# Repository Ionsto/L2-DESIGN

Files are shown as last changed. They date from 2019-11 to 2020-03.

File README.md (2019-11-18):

# L2-DESIGN
 Level 2 design coursework, electric skateboard

PLEASE USE THE FOLDER STRUCTURE PROPERLY TO KEEP THINGS EASY TO FIND

USE THIS https://www.overleaf.com/edu/durham#overview get a free account \#blessed
 
## GIT
How to use git for dummies:

https://rogerdudler.github.io/git-guide/

The general idea is that you:
 - *PULL* at the start of work, make some changes locally
 - *ADD* only the key changed files
 - *COMMIT* changes with a descriptive commit message 
 - *PUSH* to give everybody else your changes

You should aim to do small and often commits vs large dumps of changes.
This allows merges to happen easier, and makes everybody life easier.

The Git workflow:

https://www.atlassian.com/git/tutorials/comparing-workflows

The heart of the git system is commits, they are your changes, and they have messages describing what youve done.
How to write a great commit message:

https://chris.beams.io/posts/git-commit/

## LaTeX

Compiled markup language, the compiler can be easily installed via TexMaker.

Resources for latex:

Overleaf has a great set of resources for learning latex, I would recomend you write text - then when you need to know a specific feature look it up.\\
- https://www.overleaf.com/learn
- https://www.overleaf.com/learn/latex/Learn_LaTeX_in_30_minutes#The_preamble_of_a_document

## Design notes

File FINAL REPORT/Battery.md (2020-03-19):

# Battery section outline
First section is headings and sub topics
## Headings
- Introduction
- Capacity
- Charging
- Control system
- Disposal  
# Direction 
### Introduction
- Actual configuration 
- Need for a battery
- Battery types
- Estimated capacity
- Estimated size and volume
### Capacity
- Range
- Gradient
- Estimated efficiency 
- Size
- Weight
- Off the shelf solutions
### Charging
- Dangers
- Mitigations
- Voltages
- Currents
- Charging times
- Use of pre-built chargers
- Need for a parallel - series mux
### Charging MUX
- Whats the purporse
- What are the key goals (safty, supplying power, allowing safe charging)
- Overview of mux circuitry
- Switching technolog
### Control system
- Seperate power supply
- Monitor charge cycles and battery health
- Wake up and monitor voltages
- Control supply MUX
- 
### Disposal
- WEEE
- Take back scheme
- Maintanance and takeback

# Nomenclture:
- S rating for batteries - how many cells in series
- Gravometric density, Wh per kg
- Volumetric density, Wh per litre 

# Direction
## Introduction 
- Battery pack is made of two smaller 6S batteries - battery voltage has increased since the feasiblity report
- Batteries are integral to eletric vehicles
- We chose lithum polymer, much better current suuply and lifespan compared to other chemistrys.
- Estimated minimum capcaity ~180Wh from feasibilty report
- We are going to be useing off the shelf batteries: XXXX XXXX
- Two battereies required to reach line voltage ~50V
- Each battery is aproximately the size xxx,xxx,xxx mm
## Capacity
- Each battery has a caoacity of ~180Wh
## Charging
- Lithium polymer is very dangerous, lots of mitigations requried to make them "safe" see faliure mode analysis
- Instead of designing and building a charging circuit - use an off the shelf solution
- We are going to use an afordable charger, model XXX which can charge one battery in X hours.
- The charger can only charge at a rail voltage of 24V - so our two batteries need to be chaged parralel
- We will need a system to take them from series to parrralel
## Control system
- To control the battery system we need an independent control system
- The control system will be based around a low power microcontroler
- There are 4 states as shown in the control flow diagram
- The control micro will monitor the battery pack and will control the series/parralel state.
- The mux will be eletrically controled and isolated from the battery micro
- The control circuit will have a serial connection to the drive micro - along with a heartbeat connection
## Battery mux
- Mux circuitry
- How the mux will make the circuit safer
- The charger can't charge in series - voltage is too high
- The balancing leads are required to keep the cells from degrading from overdischarge
- Switching technology chosen is solid state power switches (high side switching fet based systems).
- Fets > Relays and mechanical switches as they are resistant to vibration and wont contact weld shorted

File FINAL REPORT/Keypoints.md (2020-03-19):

# Key points we want to talk about for the report
## Introduction
## Business case
## Decision matrices

## Drive belt

## Battery

## Electrical control systems

## Final words

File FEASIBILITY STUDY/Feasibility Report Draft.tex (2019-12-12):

\documentclass[journal,10pt]{IEEEtran}
\usepackage{amsmath}
\usepackage{graphicx}
\usepackage{float}
\usepackage{comment}
\usepackage{setspace}
\usepackage{caption}
\usepackage{hyperref}
\usepackage[T1]{fontenc}
\doublespacing
\title{ 
\begin{huge}
\textbf{L2 Design Feasibility Report: Electric Skateboard} 
\end{huge} }
\author{Toby Ashton, Jacob Black, Hugo McCartney, Haydn Lisk, Edward Street, Sam Sutcliffe}
\begin{document}
\maketitle
\tableofcontents
\newpage
\section{Executive Summary}
        This project concerns the design and construction of an electric skateboard based on a traditional longboard.
\section{Introduction}
        This project's scope consists of designing an electric skateboard capable of carrying a large male for daily transport. A longboard was supplied which will be modified to produce the final product. 
\section{Board}
    \subsection{Overview}
        The board provided was a 'Mindless Raider I model (34’’ x 8’’)’\cite{boardModel}. The deck was modelled in SOLIDWORKS and assembled with a library model of the trucks \cite{trucksCAD} - this allowed a Finite Element Method (FEM) analysis to be performed. Material properties were taken for maple wood, as it is the main board material. Fig \ref{fig:Board_Rendering} shows a rendering of the final concept \cite{shoesCAD}. 
        \begin{figure}[H]
                \centering
                \scalebox{0.25}{}
                \caption{
                Rendering of Skateboard}
                \label{fig:Board_Rendering}
            \end{figure} 
    \subsection{Component Arrangements}
        Several arrangement options for the electrical components were explored, subject to the following limiting factors:
        \begin{itemize}
            	\item Ground Clearance
            	\item Transmission Efficiency
            	\item Balance 
            	\item Rider Comfort
            \end{itemize}
        \begin{figure}[H]
                \centering
                \scalebox{0.30}{}
                \caption{Concept A}
                \label{fig:ConceptA}
            \end{figure} 
        \begin{figure}[H]
                \centering
                \scalebox{0.19}{}
                \caption{Concept B}
                \label{fig:ConceptB}
            \end{figure}  
        \begin{figure}[H]
                \centering
                \scalebox{0.19}{}
                \caption{Concept C}
                \label{fig:ConceptC}
            \end{figure} 
        \begin{figure}[H]
                \centering
                \scalebox{0.19}{}
                \caption{Concept D}
                \label{Fig:ConceptD}
            \end{figure} 
        \begin{figure}[H]
                \centering
                \scalebox{0.19}{}
                \caption{Concept E}
                \label{Fig:ConceptE}
            \end{figure}
    \subsection{Structural Analysis}
        %Rider load was assumed to total 1100N, applied over two 10cmx10cm areas at appropriate positions on the board. An additional load of 80N was applied at the centre of the wheelbase to model the weight of the electrical components.The simulation computed the maximum Von-Mises stress to be approximately 31.69MPa, located at the joint between the truck and the board, as shown in the figures below.
        \begin{figure}[H]
            \centering
            \scalebox{0.3}{}
            \caption{FEM Von Mises Stress Analysis of Top Surface of the Board
            }
            \label{fig:stressTop}
        \end{figure}
        \begin{figure}[H]
            \centering
            \scalebox{0.35}{}
            \caption{FEM Von Mises Stress Analysis of Bottom Surface of the Board
            }
            \label{fig:stressBottom}
        \end{figure}
        %Comparing this to the yield strength of maple wood, approximately 65.5MPa \cite{materialProperties}, a Factor of Safety value of approximately 2.1 was calculated. A further simulation was performed with the rider's load scaled up by this FOS, and the load located at a single 10cmx10cm area at the centre of the wheelbase. Maximum displacement was calculated as approximately 18.19mm (shown below). 
        \begin{figure}[H]
                \centering
                \scalebox{0.35}{}
                \caption{Displacement Contour of Board When Put Under Maximum Loading
                }
                \label{fig:Displacement}
            \end{figure}
        %With the unloaded board height of 110mm, this allows a minimum ground clearance of approximately 91.8mm - this was considered acceptable as the electrical components will have a max height of 45.9mm considering a FOS of 2.
    
\section{Powertrain}
    \subsection{Transmission}
        \subsubsection{Gearing}
            Gears provide a vast array of gear ratios but the large range of output speeds of motors makes large gear ratios unnecessary.
        \begin{figure}[H]
            \centering
            \scalebox{0.125}{}
            \caption{Arrangement with gears}
            \label{fig:DrivetrainChain}
        \end{figure}
        \subsubsection{Hub Motor}
            Hub motors are contained in the wheels of the skateboard, offering many advantages including quietness, low maintenance and sleek appearance.
            However as they have no gearing and have limited space, they provide less torque than other drives. %\[cooling?, wheel customization, ride- thin polyurethane]
        \subsubsection{Chain}
            Using a chain drive is the most efficient way to transmit power amongst the options covered, with a typical efficiency of 98\%. \cite{Mechanical_Power_Transmission} However, high maintenance is required due to the need for lubrication to prevent wear and corrosion. 
        \subsubsection{Belt}
            Due to the elasticity of toothed rubber belts, this option provides low noise and vibration, and efficient power transmission. Furthermore, they require relatively low maintenance and have a long lifespan making this preferable.
        \begin{figure}[H]
            \centering
            \scalebox{0.14}{}
            \caption{Arrangement with Belt or Chain}
            \label{fig:Drivetrain2}
        \end{figure}
        \begin{figure}[H]
            \centering
            \scalebox{0.13}{}
            \caption{Arrangement with Belt attached to trucks}
            \label{fig:Drivetrain3}
        \end{figure}
        
    \subsection{Motor}
        \subsubsection{Required Parameters}
        The main requirements of the motor at 8$ms^{-1}$, with a slope of 10$^{\circ}$ and 1$ms^{-2}$ acceleration using equations bellow are:
        \begin{itemize}
        	\item Size- The motor must fit under the board and be relatively lightweight
        	\item Torque- 13Nm at the wheel 
        	\item Speed- The $K_{v}$ motor parameter should be 250 eqn
        	\item Power- 2000w assuming no acceleration uphill at 8$ms^{-1}$
        \end{itemize}
        \begin{figure}[H]
            \centering
            \scalebox{0.5}{}
            \label{fig:equations}
        \end{figure}
        
        %\begin{gather}
        %    F = F_{Rolling Resistance} + F_{Acceleration} + F_{Gravity}\\
        %    F_{Acceleration} = Mass \times Acceleration\\
        %    F_{Gravity} = Weight \times sin(Slope Angle)\\
        %    F_{Rolling Resistance} = 4.64N\\
        %    Torque = F_{Total} \times R_{Wheels}\\
        %    Wheel RPM = \frac{Velocity (ms^{-1})}{Radius}\times \frac{60}{2\pi}\\ 
        %    Motor Power = \frac{F_{Total} \times Velocity (ms^{-1})}{Efficiency}
        %\end{gather}
        \subsubsection{AC Motor}
            AC induction motors have excellent efficiency, reliability and durability. However, using DC supply would require a variable frequency inverter to produce AC speed control. 
        \begin{figure}[H]
            \centering
            \scalebox{0.25}{}
            \label{fig:AC_Curve}
            \caption{AC Motor Curve \cite{AC_Motor_pic}}
        \end{figure}
        \subsubsection{DC Brushed Motor}
            Using a commutator allows a motor to be run from a DC supply but using carbon brushes adds a large amount of friction and varying the speed of this type of motor is harder, especially if two motors were implemented and run synchronously.
        \subsubsection{DC Brushless Motor}
            With an electronic speed controller a motor can be run from a DC supply with speed control and without a commutator meaning less friction so greater efficiency, longer lifespan and reduced weight for the same output power. This motor family also gives a large staring torque, enabling the board to accelerate quickly at low speeds \cite{AC_Motor}. For these reasons it was decided a DC brushless motor would be used.
    \section{Battery}
    A compact and quickly rechargeable battery is required. A supply rail of 24V is common for consumer electronics and will not require high voltage safety precautions. Battery charge capacity (amp-hours) and energy capacity are used roughly interchangeably due to the constant supply voltage for ease of calculation but will be annotated with the units strictly.
        \subsubsection{Capacity}
            The larger a battery network's capacity, the heavier and more expensive it becomes.Two main considerations regarding required capacity are range and lifespan. Range is be determined by average daily usage (a 1.5 km round trip between Butler and Science sites, (Fig. \ref{fig:route}) and expected charge frequency (assumed once a week).
            \begin{figure}[H]
                \centering
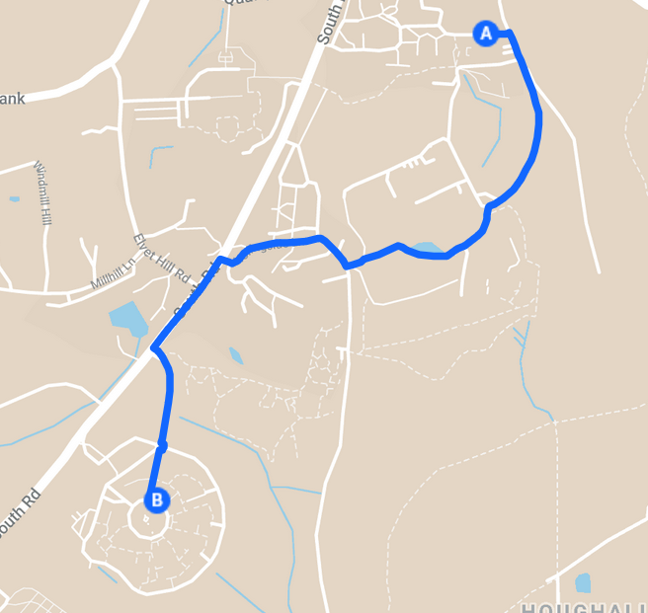
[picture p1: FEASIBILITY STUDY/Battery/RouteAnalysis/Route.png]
                \scalebox{0.5}{}
                \caption{Typical Daily Route}
                \label{fig:route}
            \end{figure}
            Extra energy considerations will be needed for the range as there is a relatively large height change throughout the route.
            Elevation and gradient variations can be seen in the graphs below, with data sourced from various GPS public databases via an online website \cite{GPSDatabase}.
            Fig \ref{fig:elevation} shows the elevation of the route and makes a difference for the maximum capacity needed.
            Fig \ref{fig:gradient} shows the gradient of this route, which will effect the maximum torque required.
            \begin{figure}[H]
                \centering
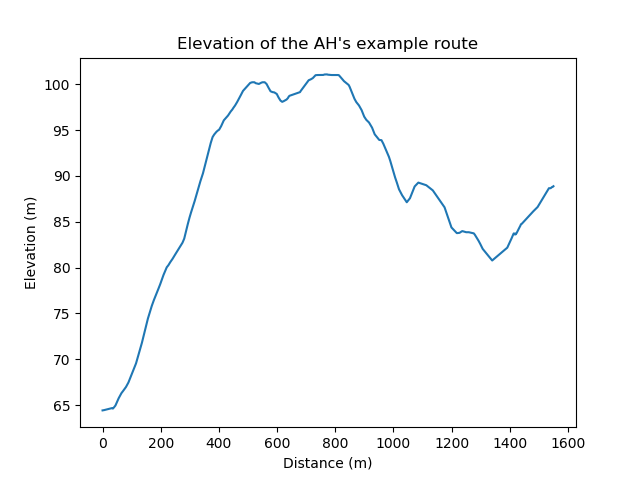
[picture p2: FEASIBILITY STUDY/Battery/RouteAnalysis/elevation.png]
                \scalebox{0.5}{}
                \caption{Elevation of Route}
                \label{fig:elevation}
            \end{figure}
            \begin{figure}[H]
                \centering
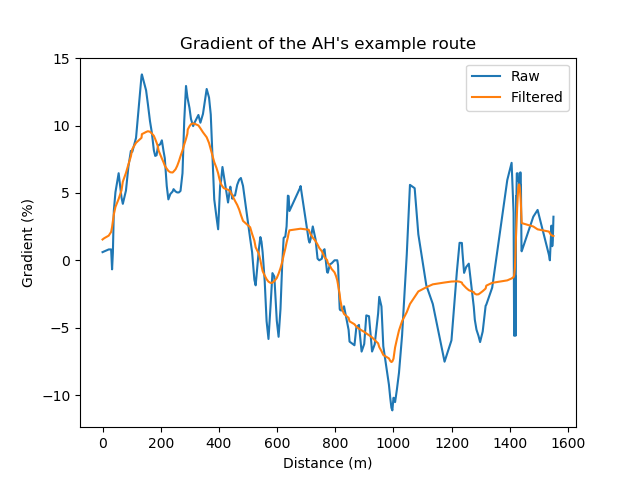
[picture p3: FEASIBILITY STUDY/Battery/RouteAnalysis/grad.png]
                \scalebox{0.5}{}
                \caption{Gradient of Route}
                \label{fig:gradient}
            \end{figure}
            Total elevation change consists of 50m uphill and 25m down (heading south). Energy requirements are modelled as a simple vehicle hoist to give an estimate (Energy = $mg\Delta h$). Total vertical ascent over the trip is 75m, so approximately 90kJ (25Wh) more energy will be required than with a flat route.
        \subsubsection{Energy Requirement Estimates}
            10Wh/mile (based off electric bike: 12Wh/mile)
            Total Energy of Journey (including vertical): 37Wh
            Per Week Consumption: 5 x 37.5Wh = 185Wh
            -Absolute Minimum Required Capacity of 185Wh
        %\subsubsection{Charging}
            %Charging the battery is a complex concern, as specific charging circuits are required to prevent damage to the system. This is particularly true of modern batteries due to the large release of heat associated with large energy transfers.
        \subsubsection{Lifespan}
            \begin{figure}[H]
                \centering
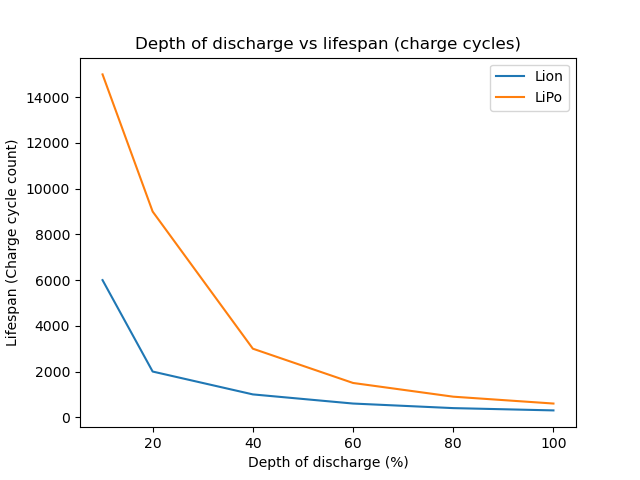
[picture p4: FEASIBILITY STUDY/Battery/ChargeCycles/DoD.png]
                \scalebox{0.5}{}
                \caption{Lifespan vs DoD (Depth of Discharge)}
                \label{fig:DoD}
            \end{figure}
            \cite{BatteryLifespan} 
            \ref{fig:DoD} illustrates the superior lifespan at comparable discharge depths.
            Lithium-ion batteries have a life cycle of approximately 800 cycles at 50\% DoD, whereas Lithium Polymer cells perform better at approximately 2000 charges at the same DoD - we will be using LiPo for this reason. Given that the capacity required at 100\% DoD is 185Wh, a 370Wh capacity is needed to achieve 50\% DoD for a full use.
        \subsubsection{Rate of Charge}
            Lithium polymer charges at a constant rate until near capacity, at which they slow down exponentially. General guidelines suggest that the charge rate should not exceed 1C [charging the total charge in one hour] to ensure optimal battery life. Ideally, the battery will charge from 50\% to full overnight. This will be achievable at a sub 1C rate [15 amp charger], which allows it to recharge from consumer wall sockets.
        \subsubsection{Battery Size}
        Battery volume and weight are limiting factors wrt. capacity. Volume affects how the components can be arranged on the board, while weight directly impacts the board's performance.    
        Using the calculated capacity the volume and mass can be calculated with the volumetric \& graviometric density. Using values from \ref{fig:Battery Size}, the volume comes to about 1.2 Litres with a mass of 2.3Kg.
            \begin{figure}[H]
                \centering
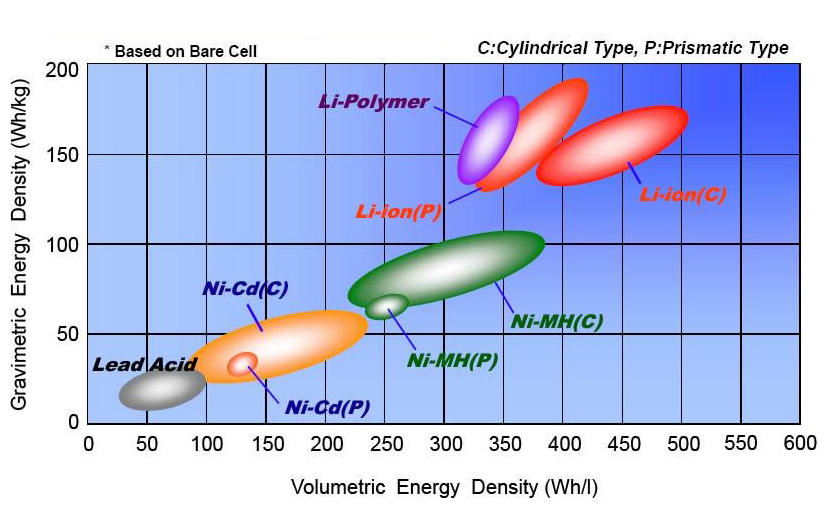
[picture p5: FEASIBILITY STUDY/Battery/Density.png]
                \scalebox{0.40}{}
                \caption{Battery size and energy density \cite{BatteryDensity}}
                \label{fig:Battery Size}
            \end{figure}
\section{Trucks}
    \subsection{Operating Terrain}
        The board will be operating over mostly smooth surfaces - however, disturbances such as uneven patches of road, litter and debris will still be present. At high speeds, low frequency oscillations (4-10Hz, called 'speed wobble' \cite{speedwobble}) build and begin to impede rider control. A suspension system is thus required to minimise these effects.
    %\subsection{Speed Wobble}
        %This phenomenon consists of unpredictable vibrations (approx. 4-10Hz) induced in the board when running at high speed – if neglected, these oscillations could directly affect the user’s ability to control the board, reducing rider comfort and potentially resulting in injury. 
    \subsection{Potential Solutions}
        Buying existing truck suspension systems would free up development time, however due to availability constraints, a bespoke design may be necessary.
        Several patented designs exist, as shown in figures \ref{fig: Spring Idea}, \ref{fig: Seperate Spring Idea} and \ref{fig: Hanger Idea}. Fig.\ref{fig: Spring Idea} shows an ideal solution, with the decision to purchase or manufacture being dependent on labour and budget constraints yet to be determined.
        \begin{figure}[H]
            \centering
            \scalebox{0.22}{}
            \caption{%Credits: Seismic Skate 
            Shock Absorber Suspension
            \cite{spring_idea} \cite{shockabsorber}}
            \label{fig: Spring Idea}
        \end{figure}
        \begin{figure}[H]
            \centering
            \scalebox{0.22}{}
            \caption{%Credit: US Patent 4,176,850 'SKATEBOARD TRUCK WITH INDEPENDENT WHEEL SUSPENSION'
            Independent Wheel Suspension
            \cite{separate_spring}}
            \label{fig: Seperate Spring Idea}
        \end{figure}
        \begin{figure}[H]
            \centering
            \scalebox{0.5}{}
            \caption{%Credit: Avenue Trucks 
            Hanger Suspension
            \cite{hanger}}
            \label{fig: Hanger Idea}
        \end{figure}
\section{Wheels}
    \subsection{Overview}
        Various factors affect the wheel design – rolling resistance is affected by the wheel and bearing materials, with torque transferred dependent on the radii and material of the driven wheels.
    \subsection{Wheel Materials}
        Longboard wheels are typically made from polyurethane, which achieve a $\mu_{rolling}$ in the range 0.04-0.08 \cite{wheel_data}. While this is sufficiently small to provide low rolling resistance (see calculations below), polyurethane only provides a $\mu$-static of ~0.2, limiting the torque that can be transferred to the road. This can be improved by using rubber for the driven wheels as rubber achieves a $\mu$-static in the range of 0.35-0.45, providing an increase in torque transmitted of 75-125\%.
    \subsection{Bearing Materials}
        Longboard bearings come in three different material families: steel, titanium and ceramic. Ceramic (Silicon Nitride) has a Brinell hardness 1479 $kg/mm^{2}$ \cite{ceramic_data1}, approximately 640\% greater than AISI-52100 steel \cite{steel_data} and ASTM-7 Titanium \cite{titanium_data}, leading to reduced energy loss from elastic deformation.  However, Silicon Nitride exhibits a yield strength of 170MPa \cite{ceramic_data2}: approximately 64\% less than steel and titanium. Ceramic is thus inadvisable as the board will be used in an environment where it is expected to suffer shocks. Additionally, ceramic bearings cost significantly more than steel and titanium, the former often in the \$90-\$150 range, as opposed to \$15-\$20 and \$30 for steel and titanium respectively. As steel and titanium perform similarly, the latter’s corrosion resistance suggests that it is the optimal type as less maintenance will be required. 
    \subsection{Wheel Dimensions}
        Longboard wheels vary in diameter between 60-100mm with a contact-patch width of approx. 30mm. Larger wheel radii provide greater top speed and smoother ride, with smaller radii producing greater mechanical advantage. 
        Wheel diameter is selected to provide the desired torque when driven by the chosen motor.
        %Depending on the output of the motor and the required road-torque, the appropriate wheel size can be selected.
    \subsection{Estimates of Rolling Resistance}
       % \begin{equation*}
       % \resizebox{\columnwidth}{!}{%
           % $F_{resistive} = (\mu _{static}  -  r_i sin(\alpha) \cos(\arcsin(\frac{r_f}{r_i}))  +  r_f %cos(\alpha)(\frac{F_{load}}{r_o – r_i})$%
    %        }
    %    \end{equation*}
    \begin{figure}[H]
        \centering
        \scalebox{0.45}{}
        \label{fig:WheelEquations}
    \end{figure}
    %Static
    %$F_{res-rubber} \approx 10.98N	
    %\\*F_{res-polyurethane} \approx 4.88N
    %\\*F_{res-total-static} = 2 F_{res-rubber} + 2 F_{res-polyurethane} = 31.72N $
    %\\*Dynamic
    %\\*$F_{res-rubber} \approx 0.37N	
    %\\*F_{res-polyurethane} \approx 1.95N
    %\\*F_{res-total-dynamic} = 2 F_{res-rubber} + 2 F_{res-polyurethane} = 4.64N$
    \cite{Combined_Resistance} 
    
\section{Control}
    \subsection{Overview}
    	Complex electronic systems require control units for operation.
    	Three aspects of control must be designed for; the user interface, battery management, and motor/drive train control.
    	In this application, the one-off nature of the product lends itself to use a micro-controller for control, rather than bespoke hardware. Microcontrollers can alter their functionality with speed and ease, due to the volume of support documentation available. Due to time and budget constraints, it may prove more effective to use existing circuit modules such as these than implementing a bespoke design.
    \subsection{User Interface}
        \begin{figure}[H]
            \centering
            \scalebox{0.2}{}
            \caption{Market Leader's Remote Control}
            \label{fig:Boosted Remote}
        \end{figure}
        \begin{figure}[H]
            \centering
            \scalebox{0.2}{\includegraphics{"./Control/Pressure Pads
            Labelled".png}}
            \caption{Dual Pressure Pad Control}
            \label{fig:Pressure Pads}
        \end{figure}
            
    	\subsubsection{Throttle Control}
    	    To ride safely, the user requires rapid and intuitive speed selection.
    		The market leader utilises a handheld wireless controller (as shown Fig.\ref{fig:Boosted Remote} \cite{BoostedRemote}) which also relays status information to the rider.
    		A potential solution to this is a dual pressure pad control system, pictured in Fig.\ref{fig:Pressure Pads} \cite{PressurePads}.
            
    	\subsubsection{Status Meters}
    		The rider must know the remaining range/time of the board. The current market leader uses an array of LEDs on its controller for status information. This can be improved by using 7 segment displays or a small LCD, allowing for quantitative data to be shown to the rider. (shown in Fig.\ref{fig:7 seg} \cite{7seg} and Fig.\ref{fig:LCD} \cite{LCD}).
    		
    	\begin{figure}[H]
            \centering
            \scalebox{0.4}{}
            \caption{7 Segment Displays}
            \label{fig:7 seg}
        \end{figure}
    	\begin{figure}[H]
            \centering
            \scalebox{0.4}{}
            \caption{Arduino LCD}
            \label{fig:LCD}
        \end{figure}
    \subsection{Battery Management}
    	Care must be taken to ensure that during normal operation the battery is charged safely.
    	This includes tracking the number of charge cycles, as well as the temperature, with a view to disabling the system if the battery is no longer in a safe state.
    	
    		%General guidelines suggest charging at no faster than 1C for optimal battery lifetime, meaning a 1300maH battery is charged at 1.3A for a duration of 1 hour.
    		%Discharge ratings vary depending on the battery, a typical hobby grade battery used for multi-rotors and helicopters boast a continuous draw of 40-50C, with a 10s burst of 90-120C, much higher than the charging rating.
    		%The number of cycles must be counted, as well as the current battery temperature to ensure that the battery is in a healthy state whenever in use.
    		%This includes preventing charging when the battery has reached the end of its operational lifetime.
    		%If regenerative braking is pursued, the circuitry must be carefully controlled so that the charging current is not exceeding these values.
    \subsection{Motor Control}
    		Since a DC Brushless motor is being used, more complex control methods are required compared to DC brushed motors.
    		This circuitry is available off the shelf, called 'Electronic Speed Controllers' and are available in a range of specifications.
    		Control of these circuits is by pulse width modulation or serial interface, varying by manufacturer, signals that can be generated simply with a microcontroller.
    		This circuit could be designed by hand, however due to complexity, and competitive pricing, it may prove a more effective choice to purchase an existing ESC.
    	%\subsection{Feedback}
    		%text goes here 
\section{Conclusion}
From our research, a number of design conclusions have been drawn: a belt-drive and brushless DC motor were selected for optimal efficiency, while rubber wheels were chosen for the driven axle due to their improved grip over polyurethane. Titanium bearings offer a compromise between performance and durability, with the final component layout providing the optimal trade-off between efficiency, ground clearance and rider comfort.

\bibliographystyle{IEEEtran}
\bibliography{IEEEabrv,bibliography.bib}

\end{document}

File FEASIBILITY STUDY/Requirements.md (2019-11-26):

# Project key points
## Requirements
- Makes minimum distance in one charge
- Hold max load - 1000N
- Charges overnight
- Constant speed uphill (South road 12% grad)
- Throttle control & dead mans switch
- Battery metre
- Easy / limited maintenance
- Waterproof housing for electronics
- Safety
  - Components secured safely
  - Suspension to protect against small bumps
- Comfortably portable / light enough to carry
- Driven wheels must provide sufficient grip for efficient power transfer
- Driven wheels achieve sufficient torque at road surface to propel board
- Non-driven wheels must provide low resistance whilst retaining ability to steer
- Bearings must provide minimal resistance to motion and be capable of withstanding stresses of normal operation

## Desired
- Goes further with one charge
- Holds more load (i.e backpack & laptop)
- Fast charging sub 1 hour
- UI, Variable speed, Acceleration control, low power control (wireless handheld device) 
- No extra lubricating needed
- Corrosion resistant
- Nice efficient housing - protective casing
- Varying suspension (manual or active)
- Efficient suspension for smooth rides
- Mass less than 10kg
- Bearings should require as little maintenance as possible
- Wheels should be durable enough to require infrequent changes
- Wheels should be capable of running on non-concrete/tarmac surfaces for short periods

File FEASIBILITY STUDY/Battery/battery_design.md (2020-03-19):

# Battery overview
## Battery picked
Two 6S batteries are more affordable to find, and allow for the batteries to be placed in disparate locations
There is also the thermal dissapation benifits for having two seperate batteries.
We picked this battery as it has roughly half the voltage we needed, and was small enought that it could fit in the encolsure.

https://www.banggood.com/ZOP-POWER-22_2V-8000mAh-60C-6S-Lipo-Battery-With-XT60-Plug-For-RC-Model-p-1328629.html

Stats:

- Watt hour capacity: 177.6Wh each
- Cell count: 6S
- Voltage: 22.2V
- Size: 90x46x158mm
- Mass: 1.24Kg

2 batteries in parallel, 355.2Wh

The batteries will be in series, so the capacity will be 178Wh together, but the operating voltage will be will be 44.4V.

## Battery charging
https://electronics.stackexchange.com/questions/115795/charging-batteries-in-parallel-when-they-are-connected-in-series-in-the-circuit
Since we have two seeprate batteries that are being used in parralel, we will either need a charger that can handle a 12S system or we will have to do some TDMA parralel charging.
https://www.flitetest.com/articles/Parallel_Charging_Your_LiPo_Batteries
Charger: CHANGED
https://www.banggood.com/ToolkitRC-URUAV-M800-300W-15A-DC-Smart-1-8S-Lipo-Battery-Balance-Charger-Discharger-With-Voltage-Servo-Checker-Receiver-Signal-Tester-Quick-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
This charger has a higher current rating - to drop charge times (did some more maths).
OLD charger: https://uk.banggood.com/SKYRC-e680-80W-8A-ACDC-Balance-Charger-Discharger-for-1-6S-Lipo-Battery-p-1526977.html?ID=47184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

## Battery charging mode 
When in operation, the  batteries are in series to get the correct operating voltage, but for charging they need to be in parralel for the charger to work.

## Battery microcontroller
Low power, separate coin battery supply, min lifespan 5 years
https://www.digikey.co.uk/product-detail/en/stmicroelectronics/STM8L152C6T6/497-10512-ND/2269726

Power supply CR2032 - 225 mAh, 3V nominal

LED indicator:

- Off - hibernating
- On - functioning
- Blinking - dead

Battery status monitor:

- 2 ADC, voltage
- 1 Ammeter, current

Battery capacity line, report both battery voltages to arduino
Battery draw line, report current usage

## Battery states
Battery system state

- Hibernation (battery isolated,LED indicator)
- Idle state (battery live, V+S,V-S, V+P, V-P all off)
- Charge state (V+P, V-P on, V+S,V-S off)
- Drive state (V+P, V-P off, V+S,V-S on)
- Battery disabled state (All off, LED indicator) - wake Arduino state reason?

## Battery switch
Used multiple N channel power MOSFETs as a high side switch

Use gate drivers: https://www.analog.com/en/about-adi/news-room/press-releases/2017/fast-60v-high-side-n-channel-mosfet-driver-provides-100-duty-cycle-capability.html
LTC7004 

Use power mosfets
FDC6324L

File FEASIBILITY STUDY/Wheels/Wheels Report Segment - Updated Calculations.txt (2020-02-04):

Wheels Section
Many factors affect the choice of wheels – rolling resistance is affected by the materials of the
wheels and bearings, with the ability to transfer power dependent on the radii and material of the
driven wheels.
Commercial longboard wheels are typically made from polyurethane, with construction normally
consisting of a hardened plastic core with the outer layers and surface of polyurethane. This material
achieves a μrolling in the range of 0.04-0.08 – while this is sufficiently small to provide low rolling
resistance, polyurethane also only provides a μstatic of ~0.2, limiting the amount of torque than can
be transferred from the motor to road surface. This can be ameliorated by using rubber for the
driven wheels as rubber achieves a μstatic in the range of 0.35-0.45, allowing for an increase in torque
transmitted of 75-125%.
Bearing materials for longboard wheels come in three different material families: steel, titanium and
ceramic. Whilst exact values of frictional resistance are difficult to find, comparisons can be
extrapolated from their material properties. Ceramic (Silicon Nitride) has a Brinell hardness 1479
kg/mm2, an increase of approx. 640% over that of AISI 52100 steel and ASTM 7 Titanium 1. This would
suggest much less energy lost from elastic deformation. However, Silicon Nitride also exhibits a yield
strength of 170MPa: approx. 64% less than steel and titanium. As such ceramic may be unadvisable
as the board will be used in an environment not dedicated to skateboarding and is likely to suffer
various shocks. Additionally, ceramic bearings cost significantly more than steel and titanium, the
former often in the $90-$150 range, as opposed to $15-$20 and $30 mark for steel and titanium
respectively. Due to the similar properties of steel and titanium bearings, the latter’s corrosion
resistance may suggest that it is the optimal of the three, increasing savings in the long-run by
requiring less maintenance.
Longboard wheels typically vary in diameter between 60-100mm with a contact patch width of
≈30mm – the size of wheel can be selected to provide the required torque at ground, with the
relevant calculations shown below.
Tables and Calculations
Material

μ-static

μ-dynamic

Polyurethane
Rubber

~ 0.2
0.35-0.45

0.04-0.08
0.01-0.015

Tg = Torque at Ground

Tw = Torque at Wheel

r = wheel radius

𝑇 =

1

These specific materials are the three most commonly used in the bearings of each material type.

Resistances at Wheels
Total mass ≈ 150kg
Mass per wheel = 37.5kg
FRES = Resistive force from Wheels
Fload = 37.5kg x 9.81 = 367.9N (per wheel)
μstatic-rubber = 0.015

μstatic-polyurethane = 0.08

μbearing = 0.0015 (assumed upper bound)
μrolling-rubber = 0.45
ri = 11mm

μrolling-polyurethae = 0.2

ro = 35mm

FRES = (μstatic – risin(α)cos(arcsin(rf/ri)) + rfcos(α)) x (Fload/(ro – ri))
α = arctan(Fp/Fload)
(rf/ri) = μbearing
arcsin(rf/ri) = 0.0859° → cos(arcsin(rf/ri) ≈ 1

Static (Skateboard Stationary, Wheels not Moving):
FRES-rubber ≈ 4.9037

FRES-polyurethane ≈ 2.2757

FRES-Total-Static = 2 FRES-rubber + 2 FRES-polyurethane = 14.36N
Dynamic
FRES-rubber ≈ 0.33111

FRES-polyurethane ≈ 1.0144

FRES-Total-Dynamic = 2 FRES-rubber + 2 FRES-polyurethane = 2.691N

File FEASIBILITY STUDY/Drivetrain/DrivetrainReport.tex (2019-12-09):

\documentclass{article}
\usepackage{amsmath}
\usepackage{verbatim} 
\begin{document}
\section{Motor Choice}
Maybe an intro? 

\subsection{Required Parameters}
The main requirements of the motor are:
\begin{itemize}
	\item Size- the motor has to fit under the board
	\item Torque- There should be enough torque to accelerate uphill - 10Nm at the wheel [figure]
	\item Speed- The Kv motor parameter should be 
	\item Power
\end{itemize}

\subsection{AC Brush-less Motor}
The AC induction motor is the most common type of motor in large industrial applications as it is very efficient durable and reliable. However, using a DC battery source would require a variable frequency inverter to produce an AC output to the motor and be able to control the speed, and particularly with single phase induction motors the staring toque is very low which is unsuitable for the application of a skateboard. 

\subsection{DC Brushed Motor}
Using a commutator allows a motor to be run from a DC supply but by using carbon brushes adds a large amount of friction to the operation and varying the speed of this type of motor is harder especially if two motors were to be used as ensuring they are running at the same speed is challenging

\subsection{DC Brush-less Motor}
With electronic speed control a motor can be run from a DC supply with relatively simple control of speed. Also as this eliminates the need for a commutator there is less friction so greater efficiency, longer lifespan and reduced wight for the same output power. This motor family also gives a large staring torque so the board will be able to accelerate quickly from the start. For these reasons it was decided a DC brush-less motor would be used.

\section{Power-train}

\subsection{Belt}
Due to elasticity of rubber belts this option provides low noise and vibration and allows for efficient power transmission. Furthermore, they are very low maintenance and have a long lifespan. 

\subsection{Gearing}
Having the output of the motor go directly into a gear arrangement or a gear box would allow for a vast array of gear ratios however this would require strong gears to provide the required torque and the large range of output speeds of DC motors means a large gear ratio may be unnecessary.
\marginpar{more specific torque info}

\subsection{Chain}
Using a chain drive is the most efficient way to transmit power out of the options covered with an typical efficiency of 98\%. [REFERENCE P80 mechanical power efficiency] However it is high maintenance due to the need of lubrication to prevent wear and oxidation. 

\subsection{Hub Motor}
Hub motors are entirely contained in the wheels of the skateboard and they offer many advantages- mainly they are extremely quiet, low maintenance and have a sleek appearance. [Details]
However as they have no gear ratios and are limited in terms of space of the wheels they provide less torque than a traditional drive. [cooling?, wheel customization, ride- thin polyurethane]
\end{document}

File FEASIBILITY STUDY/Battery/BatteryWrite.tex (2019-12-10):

\documentclass{article}
\usepackage{amsmath}
\usepackage{graphicx}
\usepackage{float}
\begin{document}
\section{Overview}
Dense energy storage is a difficult task, and batteries are a must for pure electric vehicles.
\section{Capacity}
The larger the capacity of a battery network, the larger, heavier, and more expensive the battery network becomes.
The use case of the system needs to be considered for choosing a capacity.
Capacitance is normally measured in Amp-Hours, or how many hours a battery can supply the rated current at the nominal voltage of the battery.

When specifying capacity for an electric vehicle, two factors are going to be needed:
\begin{itemize}
    \item Range
    \item Efficiency
\end{itemize}
The nominal range will be determined by the expected average daily usage, and the specified charge frequency. 
The value given for charge frequency will be once a week.
The daily usage will be a round trip from Josephine butler to the engineering department on the science site each way this is ~1.5km, this is shown in Fig. \ref{fig:route}.
\begin{figure}[H]
    \centering
    \scalebox{0.5}{}
    \caption{Nominal daily route}
    \label{fig:route}
\end{figure}
The exact elevation change can be seen in \ref{fig:route_el}, with the gradients of this data in \ref{fig:route_grad}.
This data is taken from GPS public databases via https://www.gpsvisualizer.com/elevation.
The routes were made using google maps - exported to GPS route format.
\begin{figure}[H]
    \centering
    \scalebox{0.5}{}
    \caption{Gradient of route}
    \label{fig:route_el}
\end{figure}
Fig. \ref{fig:route_el} shows the elevation through the route, with mountjoy easily identifiable. 
\begin{figure}[H]
    \centering
    \scalebox{0.5}{}
    \caption{Elevation of route}
    \label{fig:route_grad}
\end{figure}
There is a total of 50 meters uphill, and 25 meters downhill when going towards butler.
The effect of the height change on the required battery capacity will be non negligible.
If we model the energy requirement as a simple vehicle hoist, the energy will be $mg\Delta h$.
The total vertical distance is 75m.
Roughly 90kJ more energy will be needed with a perfectly efficient system.
Since a joule is one watt second, 90kJ is 25 watt hours.

Rough power estimates: 
10 watt hours per mile - electric bike
12 watt hours per journey (flat)

The total Watt hours of the journey including the vertical distance is 37 watt hours.

For a 5 journeys a week
$37 \cdot 5 = 185Wh$
185 watt hours is needed to make the journey from 100\% battery to flat.

\section{Charging}
Battery charging is difficult, specific charging circuits are needed for most modern high density batteries.
When trying to charge lots of batteries quickly a large amount of heat is generated, which needs to be considered in the design stage.
Large modern batteries can also be very dangerous - and this is amplified when charging, so care needs to be taken that the design isn't a health hazard.
\subsection{Lifespan}
The lifespan of a battery is determined by the depth of discharge, and the family of battery used.
\begin{figure}[H]
    \centering
    \scalebox{0.5}{}
    \caption{Lifespan with respect to usage}
    \label{fig:route}
\end{figure}
Lithium ion batteries have a cycle life of about 800 cycles at 50\% DoD, whereas Lithium polymer does much better at approximately 2000 charges at 50\%.
For this reason we are using LiPo batteries as they offer the better battery life.
Given the capacity to 100\% DoD is 185Wh, the final capacity will need to be 370Wh.
\subsection{Rate of charge}
The rate of charging is a nonlinear function with the charge of the battery, therefore it doesn't to quote charge time from 0\%-100\%.
It makes sense to specify a rate of recharge from a specific depth of discharge.
The specific depth of discharge will be determined by the lifespan of the battery, and we can consider a "charge cycle" charging from DoD\% to 95\%.

%https://www.dnkpower.com/lithium-polymer-battery-guide/
%https://batteryuniversity.com/learn/article/how_to_prolong_lithium_based_batteries
\section{Battery size}
The battery size and weight are limiting factors on capacity.
There are two parts to battery 'size' the volume, and mass of the battery are critical factors for a moving vehicle.
\begin{figure}[H]
    \centering
    \scalebox{0.5}{}
    \caption{Credits: NASA - National Aeronautics and Space Administration}
    \label{fig:route}
\end{figure}
\end{document}

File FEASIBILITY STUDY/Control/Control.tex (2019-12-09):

\documentclass[journal,10pt]{IEEEtran}
\usepackage{amsmath}
\begin{document}
\section{Overview}
	Any complex electronic system will almost always require a control unit to operate it.
	There are three aspects of control that must be designed for; the user interface to control the skateboard, battery management, and motor/drive train control.
	For this application, and the one-off nature of the product, it would be most effective to use a micro-controller system on a chip for control, rather than a bespoke hardware solution.
	This is due to the ease of altering functionality, and the high volume of support documentation for these units.
	Due to time and budget constraints, it would also be more effective to search for existing circuit modules than trying to design and build bespoke layouts.
\section{User Interface}
	%\subsection{Overview}
		%\begin{itemize}
			%\item Throttle (Both variable and on/off)
			%\item Status meters to the rider (battery percentage, throttle level etc)
		%\end{itemize}
	\subsection{Throttle Control}
		The user needs to be able to control the speed of the board intuitively and quickly, to ensure safe riding.
		The market leader utilises wireless controller (as shown Fig XXX)allowing for braking, accelerating and reverse, with fine stepwise control for each by a roller potentiometer.
		This only takes effect when a secondary button is held, acting as a dead-mans-switch.
		A potential solution to this is a dual pressure pad system, pictured XXX.
	\subsection{Status Meters}
		The user needs to be able to understand what the remaining range of the board is, so that they will not undertake a journey where they will run out of charge mid-journey.
	The current market leader uses an array of LEDs on its controller for status information.
		This can easily be improved on using 7 segment displays or a small LCD, allowing for numerical data to be shown to the rider.
\section{Battery Management}
	%\subsection{Overview}
		%\begin{itemize}
			%\item Safe charging and discharging 
			%\item Monitoring battery health including charge cycle number
		%\end{itemize}
	\subsection{Charging/Discharging}
	***Care must be taken to ensure that in normal operation the battery is not charged or discharged outside of safe conditions.
	This includes tracking the number of cycles the battery has gone through, as well as temperature, with a view to stop the rider from using the system if the battery is no longer in a safe state.***
	
		%General guidelines suggest charging at no faster than 1C for optimal battery lifetime, meaning a 1300maH battery is charged at 1.3A for a duration of 1 hour.
		%Discharge ratings vary depending on the battery, a typical hobby grade battery used for multi-rotors and helicopters boast a continuous draw of 40-50C, with a 10s burst of 90-120C, much higher than the charging rating.
		%The number of cycles must be counted, as well as the current battery temperature to ensure that the battery is in a healthy state whenever in use.
		%This includes preventing charging when the battery has reached the end of its operational lifetime.
		%If regenerative braking is pursued, the circuitry must be carefully controlled so that the charging current is not exceeding these values.
\section{Motor Control}
	%\subsection{Overview}
		%\begin{itemize}
			%\item Types of motor that could be used, brushed vs brushless
			%\item control methods for each type, pwm vs 3 phase control
			%\item Efficiency of each method
			%\item power draw
			%\item complexity
		%\end{itemize}
	\subsection{Motor control}
		Since a DC Brushless motor is being used, a more complex control method is required than a brushed DC motor.
		This circuitry can be obtained off the shelf as an 'Electronic Speed Controller' and are widely available in a range of specifications due to their use in the remote control model industry.
		Control of these circuits is by pulse width modulation, or serial interface, varying by model and age of controller, signals that can be generated simply with a microcontroller.
		%This circuit could be designed and produced by hand, however due to the complexity, and the competitive pricing of the currently available products, it may prove a more effective choice to purchase an existing ESC.
	%\subsection{Feedback}
		%text goes here
\end{document}

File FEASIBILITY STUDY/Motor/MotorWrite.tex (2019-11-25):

\documentclass{article}
\usepackage{amsmath}
\usepackage{tikz}
\begin{document}
\section{Overview}
The motor in an electric vehicle is a major component.
The type of motor can have large design implications, from power suppieys to drive chain.
\subsection{AC motor}
An AC motor is driven by an AC current.
The motors rotation speed is set by the supply frequency and the number of poles.
The AC motor doesn't need a split ring commutator like a DC supply, but is less flexible.

The kind of motor considered would be an AC induction motor.
The system attempts to bring the rotor frequency into a value proportional to the drive frequency.

This will need a variable frequency inverter.

\subsection{DC motor}
DC motors are a class of motor driven by a DC supply.
The DC supply then needs to be driven to the rotors in an oscillatory fashion. 
These are commonly used for electric vehicles as they have the useful property of increasing torque when under load. 
\subsection{Brushed vs Brushless}
Brushless motors requires a drive control circuit to turn the supply DC into a set of oscillating drive lines.
Brushed motors have a much more simple drive system, the supply is DC, and the supply is commutated mechanically.
The brushes incur mechanical loss.

DC brushless the supply is DC, but is modulated to create the time varying supply.
Either an inverter or a power supply.

\section{Required}
\begin{itemize}
    \item Max output (Wh) can supply motor
    \item Battery lasts for 1 week of use with 1 charge
    \item Charges overnight (8 hours) at a maximum
\end{itemize}
\section{Desired}
\begin{itemize}
    \item Charges in 1 hour
    \item :
\end{itemize}

\end{document}

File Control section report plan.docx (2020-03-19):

Control section

- Motors need to be driven by an ESC
  - ESCs
  - How they work?
  - Control method and hall sensors
  - PWM explained
- Headlight LEDs
- Buzzers
- Pressure Pads
  - How to use them for control, with existing control methods discussed and explained why pressure pads were used
- LCD screen
  - Control method
- Arduino
  - Why a microcontroller is required
  - Why an Arduino is a good option
  - Design considerations due to using an Arduino
  - Control code requirements
  - The main control loop explained
- Rectifier for power supply
  - Why its needed
- Talk about electrical safety

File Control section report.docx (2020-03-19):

INCLUDE? -> MARKET LEADER BOOSTED USES 12c and also used brushless with ESCs

Modern brushless DC motors lack complexity themselves, simply constructed of 3 windings in a XXX configuration, driven by a 3 phase AC voltage. Electrical power for this project will be a battery, producing a DC voltage, therefore an inverter will be required to produce the correct drive voltages. This hardware is called an Electronic Speed Controller (ESC) and converts a DC voltage to a 3 phase AC voltage source in order to drive the motor. To use this technology in an electric skateboard, size and weight of the circuitry must be minimised, as space under the deck of the skateboard is at a premium, and any increase in the weight of the board reduces the top end speed. ESCs are a well-documented piece of circuity, and a bespoke controller could be designed specifically for the skateboard. However due to time constraints of team members it was evaluated to be more effective to purchase a pre-existing model that meets the requirements recommended by the motor manufacturer, whilst remaining compact and lightweight. The hobby remote control sector is one of the largest users of ESC technology, as a result of this market there is a full catalogue of ESCs available at a wide range of voltage and current limits, whilst remaining small and light in order that battery life can be maximised in their designed applications. Recommended rating values for the chosen motors are a maximum of 50v (DC), at a continuous current of 120A, giving a factor of safety of 1.5 for the motor’s 80A nominal current draw.

To set the motor speed, electronic control signals are sent to the speed controller, that then manipulates the characteristics of the voltages it produces to accelerate or decelerate the motor to the speed requested. There is a wide range of signal protocols used for this purpose, however the most common (and easiest to implement) is Pulse Width Modulation (PWM) where the ‘high’ period of a repeating square wave is varied between a predetermined range to signify to the controller the requested motor speed. The total time period of the square wave is maintained, resulting in the ‘low’ duration reducing as the ‘high’ duration increases, before the next wave begins. Therefore, as the total wave period decreases, the latency to the controller decreases, as the time taken to transmit a command signal is reduced. However, this signal is often sent over an unshielded wire at a logic high voltage level of 5v, making it sensitive to interference, especially in remote control applications, and therefore there is a lower limit on wave period where the signal becomes indistinguishable from background noise.

XXX

A vital aspect of the control system to consider is the method of relaying information back to the rider, in order that they understand the remaining battery and range, alongside any error states or other information. Therefore, an LCD screen is going to be used, which can display 32 characters at a time in 2 rows of 16. Data transfer to the LCD is performed using an established communication standard - Universal Asynchronous Receiver/Transmitter (UART). Text data (ASCII values) to be displayed is decoded by the LCD hardware and displayed until the next refresh signal arrives with new data. An LCD was chosen over an array of seven segment displays due to the availability of displaying letters in addition to numbers, allowing for enhanced information to be relayed to the rider. This was also in addition to the nature of the LCD arriving in a self-contained functional module, rather than having to design a controller if using a 7 segment display bank.

For the user to control the board speed, pressure pads will be used. If the rider shifts their weight forwards, the board will accelerate, and if the rider leans backwards the board will decelerate. By mapping the weight differential to a requested acceleration, the speed the motors need to turn can be calculated, and the signal sent to the ESCs for each motor. Pressure pad control was chosen rather than a remote control or a direct wire connection due to the ease of design and manufacture, as a remote control especially has a great deal of debugging and loss of signal concerns. Further to this, the system can detect when the rider dismounts, and can stop the board if required.

In order for the pressure pads to affect the system, the information represented by their varying resistances must be interpreted, and the resulting commands changing the speed of the board as required. Therefore, a central control unit must be designed, to interface with the analogue inputs, and create digital control signals the ESCs and LCD can interpret.

However, a microcontroller such as an Arduino nano is powered by a 5v supply rail, which is 10 times smaller than the 50v nominal that the motors will be running at, and therefore a method of producing this voltage is required. The hobby rc industry is again has a circuit such as this available, and a 20A maximum current rating 5v UBEC will be used, which is designed to convert a 12 cell lipo battery voltage to 5v.

The battery voltage is dangerous, running at 50v DC, therefore isolation procedures must be undertaken to ensure that they are electrically safe. Firstly, there is no point in the design where a connection at 50v DC can be accessed without removing the casing of the skateboard, which (NEED TO LOOK UP THE LAW ON HIGH VOLTAGES ETC) makes it safe blah blah blah cover it in insulation blah blah blah

TALK ABOUT FAILURE MODE ANALYSIS? ME AND SAM TOGETHER??

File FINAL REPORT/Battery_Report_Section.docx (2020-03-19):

Battery

Intro:
Batteries are an integral component in any electric vehicle, as they provide a portable energy source required for the machine to operate. The battery pack implemented in our design consists of two 6S (6 cell) batteries operating in series to generate a line voltage of 50V, an increase from the 25V specified in the feasibility report. In order to meet the user case requirements, a capacity of at least 360Wh will be required from the battery pack- this will be achieved with lithium polymer batteries of approximate dimension 90x46x158 mm. Maybe talk about commute. Lithium polymer provides superior current supply and lifespan relative to other battery chemistries, making it ideal for this application. However, as there are certain risks involved with such batteries, a ratified off the shelf implementation will be used. Below is the full schematic of the battery control unit, displaying the mux for charging and discharging, the micro-controller, error-state LED display and separate battery supply for the micro. The various components of the design are detailed in the following sections.

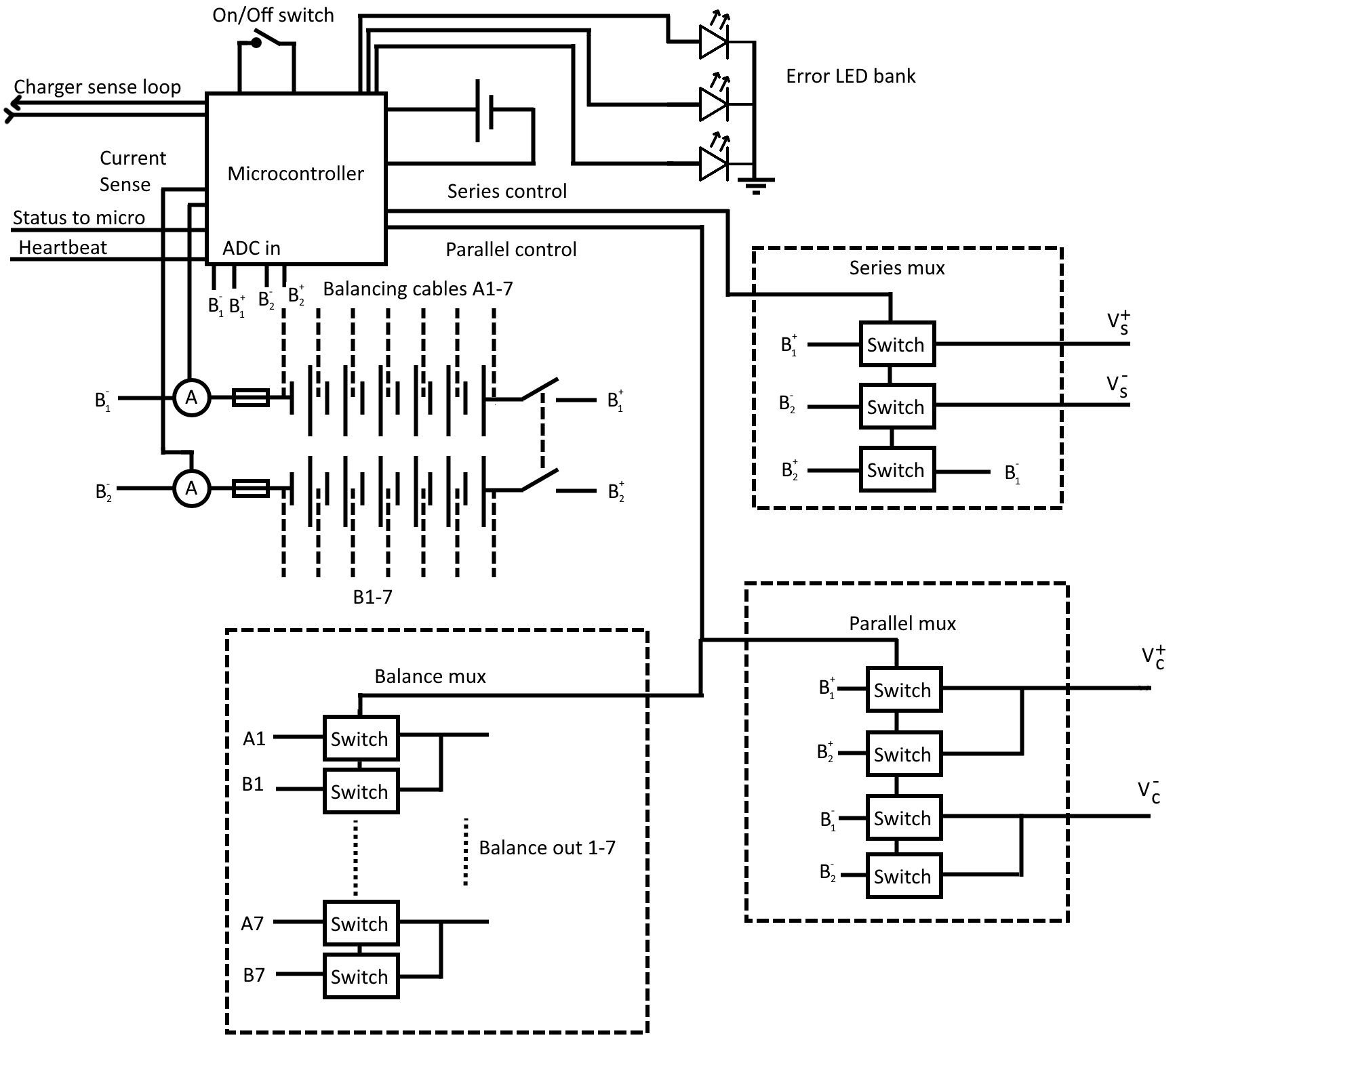
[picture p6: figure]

- Increase the serial comms to bus width

Capacity:

Various parameters affect the required range of the battery: it is specified to be charged once every 5 days whilst travelling an average distance of 3km a day, requiring a 15km range at full charge. On the flat, energy usage is estimated to be in the order of 10Wh/mile (where does this come from) – however, as a typical route is expected to contain gradients of up to 15%, the energy consumption rises to an average of 19.7Wh/mile (37Wh per daily commute). For a charge frequency of once every 5 days, a minimum capacity of 180Wh is needed. As outlined in the feasibility report, lithium polymer is the optimal battery technology for this application, with greater gravimetric energy density than other battery types. To provide the required 360Wh, the battery pack therefore would weigh approximately 2.4kg – this is a small enough load for the board to handle comfortably. The minimum energy requirement for a week’s usage was determined at approximately 180Wh – however to achieve better lifespan and provide for margin of error, the battery pack has a capacity 360Wh. This allows for an average depth of discharge of 50%, (rising to 60% with heavy usage), with each battery still holding half of its energy stored before it is recharged.

Graph of DoD here

MAKE IT MORE PROFFESIONAL SOUNDING The large capacity of the battery allows it to operate without running it flat during normal usage. High discharge levels reduce battery capacity significantly after approximately 100 cycles, severely limiting both range and battery service life. A DoD of 60% enables a theoretical lifespan of 2000 cycles, compared 300 at 100%. Due to the high current and voltage on the battery, these theoretical values will drop significantly, indicating that a DoD of 60% would be preferable as there is a significantly greater factor of safety at this discharge than when running the battery flat.

Charging:

BETTER START Due to the large battery capacity required in this application, charging becomes a significant design problem. As a large energy store is involved, the charging process must be carefully controlled not only to provide the large energy quantities, but also to prevent both damage to the battery and harm to the user.

There are various dangers associated with charging lithium polymer batteries due to lithium’s highly reactive nature: overcharging can lead to catastrophic failure in the form of fire and explosion, whilst over-discharge can lead to the formation of whisker salt deposits within the battery. Such deposits reduce coulombic efficiency and thus capacity, as well as potentially causing permanent failure if the whiskers puncture the separator, which would lead to the battery circuitry being shorted. Both overcharging and discharging can cause CO2 off-gassing, leading to the expansion and bursting of the battery casing and allowing highly reactive battery fluid to escape. As such, various mitigations must be put in place: fuses can be installed to prevent the rate of charge/discharge from exceeding safe levels whilst a battery health monitor can be implemented to ensure that the user is aware of when the battery is no longer safe for usage. Sophisticated charging circuitry must be supplied along with a detailed user manual in order to further safeguard against overcharging - such circuitry will have the capacity to monitor the battery level and reduce/increase current flow to it accordingly. To prevent discharge, an idle mode can be implemented so that the board doesn’t consume excess power if accidentally left on outside of operation. This can be further improved by means of a mechanical isolation switch, which would prevent any power being drawn the power and control circuitry when not in use.

Due to the aforementioned BETTER WORD needed dangers, it was decided that an off-the-shelf solution would be required, as designing an appropriate charging circuit for such an application in-house was not feasible. Need to push the safety reason for no 50v This however presents another problem – as the charger we picked (ToolkitRC & URUAV M800) produces 24V and cannot handle the 50V operating voltage, the batteries must be charged in parallel though they operate in series. Thus, some means of switching between series and parallel must be implemented. Additionally, this control system must include some means of balancing the charging between the multiple cells, otherwise overall capacity may be reduced due to uneven charging. IF SPACE FLESH OUT WHY

- Charger detection – shorted pins on the connector
- Custom cable – single connector for the balance leads and power rails

Control System Overview:

Due to the complex nature of the battery’s operation within this design, a control system is required to manage it. A low-power microcontroller (the STM8L) forms the basis of this system, which consists of the four control states shown in the flow diagram. This microcontroller will monitor the health of the battery pack and switch between drive (discharge) and charging by means of the battery mux detailed within the next section. This micro will receive a heartbeat signal from the main control Arduino (see control section), which will trigger the micro’s operational state. When the board is on but not in use (e.g. rider has dismounted), the micro will be able to safely isolate the battery electronics by entering the idle state, and then conserve power by moving into the hibernate state if the board remains idle for longer than a certain period of time. This micro will be on permanently in order to continually monitor the activity and health of the battery, and as such must require sufficiently low power in order for the separate battery supply to be sufficient for the product’s entire lifespan. COIN CELL The STM8L meets this requirement, requiring drawing 100μA when operational and 10μA when in a “sleep” state, which will be the case when the controller has into hibernate phase.

- Conserve power by keeping the micro on as short as possible
- Use triggers/interrupts mostly to transition from states / trigger error states

Arduino comms

- The micro also sends periodic serial transmissions to the Arduino with battery capacity and health
- The Arduino talks to the micro with a heartbeat pulse, if the heartbeat stops then the micro drops into idle imminently

Insert flow diagram here

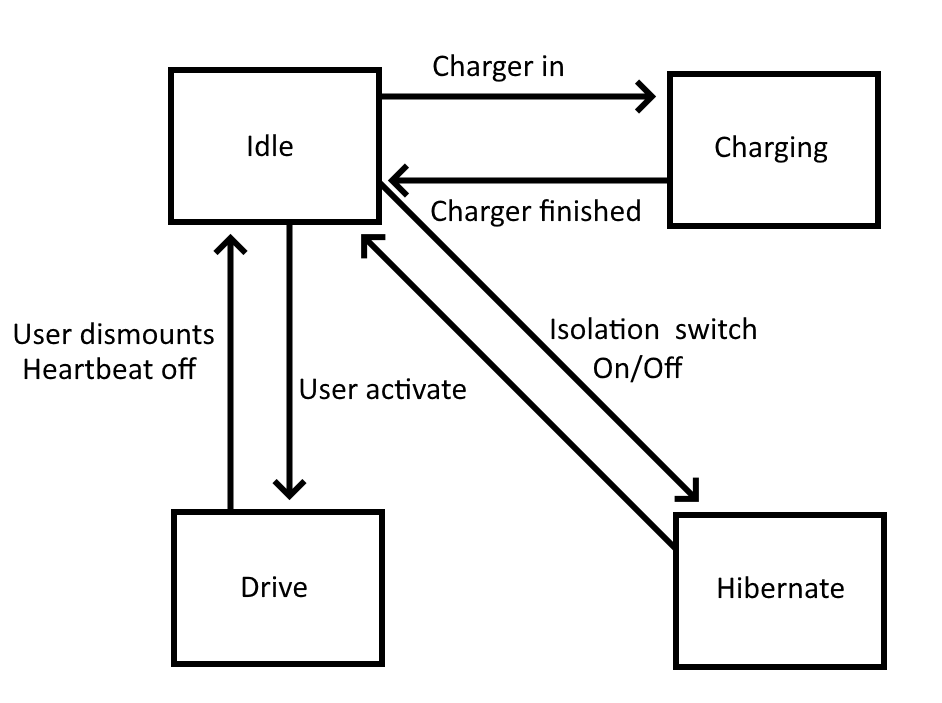
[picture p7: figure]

- Flow chart description
- Drive: the system is in drive mode – the main Arduino is on
- Hibernate: the system is mechanically isolated (the main breaker switches are off) (series)
- Idle: The muxes are off, but can transition into charging/drive
- Charge: the charger port is connected (parallel) and the charger mux is enabled

System transtitions

- Moving in and out of hibernate is done by moving the isolation switch (this is going to be hard)
- Moving from idle to charge happens when the charger is plugged in/out – if the battery monitor wants to stop charging it can forcefully disconnect the charger
- Moving from idle to drive happens when the user presses a button, if the battery monitor thinks that the battery pack is damaged this will trigger the LED error states
- The device drops from drive to idle by the Arduino controlling it with the heartbeat monitor

Battery Mux: what is a mux?

The battery itself has three states: charging in parallel, discharging in series and disconnected (in which there are no live terminals out of the battery system). To achieve this, a multiplexer was designed to handle switching between these states. As seen below, the mux has three main segments which receive input signals from the microcontroller. The series mux handles the discharge path (used in drive mode) which operates at 50V, 200A. When charging, the microcontroller activates the parallel control branch to the parallel mux which is rated at 25V and 10A. This signal also activates the balancing mux which handles seven low voltage, low current paths for equalising the power transferred to each battery cell. The micro can also (lots of alsos in this) isolate the battery electrically by simply disconnect? all the switches, putting the device in “Idle” mode – for safety reasons, this is the default state when not receiving the heartbeat signal. A mechanical switch operated by the user was considered for changing between the charge/discharge modes – whilst this was an attractive option due to its simplicity and relatively low cost, we considered it irresponsible from a design perspective to leave this in the user’s hands as the switching process is the most electrically hazardous part of the design. (explicit in why it breaks However, for switching the device in and out of hibernate mode, a dead-bolt style(vibration?) switch is implemented as the simpler nature of the electronics being controlled by this switch reduces the chance of damage being done (what damage are you talking about?).

- Severity of moving between hibernation states is low
- Probality is reasonably high
- Therefore we can allow using a mechanical switch

Sam, explain how micro selects “DISCONNECTED” state

As shown by the diagram, a great many switches are required within the multiplexer, the choice of technology regarding which is significant. There are two main candidates: relays and MOSFETs. A relay is effectively an electromechanical switch, capable of handling high currents and voltages whilst also consuming a very low standby draw. MOSFETs by contrast are solid state devices that can’t withstand currents as great as that relays and consume more power on standby. Crucially however, relays are sensitive to vibration and are vulnerable to shorting or contact-welding in this scenario. MOSFETs are resistant to such mechanical issues, and as they can operate comfortably at the rated currents and voltages of the design, are better suited to this application.

Alton also complained about not using a mechanical switch so we should add a little section

- Mechanical switches were rejected as they are also prone to the same issues as the relays
- They also need to be operated by the user – (they could forget and damage the charger itself)
- They are much cheaper and simpler to design (but come with some downsides)
- They are overall less safe – which trumps there simplicity and cost
- This switch is not used very often so it can be vibration protected, and won’t cause a catastrophic failure if it is open or close

Mechanical Considerations:

Other potential hazards include mechanical damage to the battery from potential impacts, which could lead to leakage of the fluid and potential ignition should the wall be punctured – this would be secured against through the use of an external hard casing that the battery would be fitted into with additional anti-vibration measures. Such measures would include providing padding between the battery and casing wall, with sufficient venting to prevent over-heating issues.

Finally, shortage of the terminals, though unlikely, still needs consideration as this failure mode is catastrophic with high current draw leading to potential ignition. This can be easily prevented however with the use of industry standard connectors with the fuse in series with the battery, isolated contacts and sufficient water-proofing.

Possible other states

Error LED states

- Low power LEDs are used to indicate battery error states
- The LEDs form a 3 bit array that can be used to lookup error states in the handbook/manual
- The LEDs flash when the on button is pressed if the system declines to move into drive mode

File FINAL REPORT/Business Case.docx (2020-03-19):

L2 Design: Business Case

- Target market and requirements thereof
  - Commuters: long-range distance, large charge interval, durability wrt. long term wear, retro-fit must be relatively straight forward to allow for lack of experience
  - Hobbyists: Must be retro-fittable to allow for regular skateboarding, shock resistant due to nature of skateboarding activities
- General costings and comparison to competitors

The general business case for an electric skateboard consists of product that can be used both as a viable means of transport as well as recreational activities. This allows for a broad market appeal if the design is suitably versatile - as such, it was decided early on in the design process that the device would be implemented as a retrofit, allowing for the design to be used in combination with a large variety of boards and thus appeal to a wide array of consumers. The current electric skateboard market is relatively small, indicating that there is room for start-ups like our product to compete, with the success of current market leaders such as Boosted and OneWheel showing that investing in this area is a viable business model and that such products are feasible from a design perspective.

This design is aimed broadly at two market groups: commuters and skateboarding hobbyists. As such, two user cases must be satisfied. The commuter requires a board that can capably traverse a typical commute within an urban environment, be able to climb significant gradients and possess a battery life that can comfortably manage a working week’s usage. To make this a viable means of every-day transport, the design must ensure reliability. Not only must the mechanical components be capable of withstanding long-term wear and mild impact, the electronics must be suitably protected from the elements and suitably programmed to avoid software failure and potentially catastrophic electrical faults. In contrast to the commuter, the hobbyist market consists of consumers well acquainted with skateboarding and thus the product must be compatible with conventional skateboarding activities in order to garner more than mere interest in a novelty item. Here the retrofit nature of the design is particularly significant, allowing the board to be converted from conventional to electrified and back with relative ease; not only does this allow for the hobbyist to electrify their board of choice whilst retaining access to conventional skating, the retrofit is also simple enough to allow for the commuter to carry it out with ease despite being less well-versed than the hobbyist. Whilst a certain degree of basic competence with hand tools will be required of the customer, the retrofit would certainly not exceed the difficulty of basic bicycle maintenance for example, thus it is reasonable to assume that this is well within the capability of the average consumer.

The material costs of this design run to approximately £880, with an estimated 20% increase to account for manufacturing costs bringing the final production cost per board to £1056. Market competitors of a similar specification such as Boosted Board’s “Boosted Plus” and OneWheel’s “XR” retail at £1300 and £1400 respectively, indicating that such a price range is considered reasonable by the current market, which would allow for a profit margin of approximately 20% at a retail price of £1270. As such, this product presents a viable business proposition, providing a strong profit margin at a competitive market price.

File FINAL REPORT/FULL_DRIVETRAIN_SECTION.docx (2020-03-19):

Drivetrain

Due to the highly interdependent nature of the motor and the transmission, these components were considered in tandem. The wheels constitute the final drive output, and as such affect the parameters of the motor, requiring them to be similarly considered in conjunction with the rest of the drive train.

Motor

SUMMARY

The final design uses a brushless DC motor due to its very efficient operation and relatively easy speed control, as well as being able to deliver high torque particularly at low speeds and whilst staring. They can also be powered using commercially available speed controllers with DC inputs.

PERFORMANCE CALCULATIONS

The following equations denote the required performance characteristics of the motors, based on the technical specification and board parameters. As discussed in the feasibility report, rolling resistance incurred is approximately 4.6N – this is negligible compared to the other forces the board is subjected to and has thus been neglected in further calculations.

1. Weight=150kg ⇒1470N
2. F_(weight) =mgsin(θ) = 150×9.81×sin(10)
3. F_(accelaration) =ma=150×1
4. F_(Total) =256+150=360N
5. Torque, T= F ×R
6. T_(Total) =405×0.0035=14.2Nm
7. T_(Per Motor) =(T_(Total))/(2×Gear Ratio)= 3.15Nm
8. ω=v/r =286rads^(-1)
9. P=(T_(Total) ×ω)/η= 5000W

MOTOR FAMILY

The decision process for selecting the motor type is summarised in matrix xx, The most suitable type was determined to be the brushless DC or BLDC motor : such motors have low friction in operation due to not having brushes, have high efficiencies, are quiet and have long lifespans with little or no maintenance. Furthermore, they possess excellent power to weight ratios, partly due to not having the weight of the brushes. Also, there are a wide range of different sizes and power ratings available so there are specific models that can deliver the required speed range as well as the power and torque necessary.

PARAMETERS

The requisite power output from the motors is 5000W [eqn. 9] – supplying this level of mechanical power with a single motor is unfeasible due to the size of such a motor, indicating that a dual motor system is more practical. With two motors, each will need to be able to deliver the following parameters with a gear ratio of 1:2.25 between the motor and drive wheels:

- 3.15Nm torque
- 2500w power
- 900rad/s or 8600rpm maximum rotation
- 170kv rating to deliver 8600rpm at 50v

SPECIFIC MOTOR CHOICE

Based on the required parameters, a 6374 motor (63mm diameter, 74mm length) as such motors are typically provide the above characteristics. Specifically, a pair of Torque Boards 6374 190KV motors were selected, each delivering 3150W and 3.57Nm of torque with a Kv rating of 190. These specifications allow for the fact that the torque curve is non -linear and to be able to accelerate from a stationary start on a hill there is a high starting torque is required. As this starting torque will be less than the quoted peak torque, this motor was chosen as it is able to provide the 3.15Nm required at starting and not only at peak operating point. Finally, the chosen motor has an integrated hall effect sensor, allowing for more accurate speed and position control than can be obtained from using the traditional method of measuring the back emf on the stator windings.

TRANSMISSION

SUMMARY

Power to the wheels of the skateboard will be delivered using a high torque rubber belt transmitting the power from a brushless DC motor to the wheels.

MOTOR CONFIGURATION AND TRANSMISSION CHOICE

The decision to not use a motor attached from the truck directly to the wheels (direct drive), or a motor built into the wheels (hub motor), is summarised in the decision matrix xx. Both of these methods were dismissed, as they would severely limit the size and thus performance of the motors that could be implemented, leaving the board incapable of traversing the 15% gradients inherent in the user case. This problem is compound by the lack of room for gearing that could provide the required torque. Hub motors were deemed particularly unsuitable due to their poor heat dissipation, which would become a major problem given the high-power output required.

To enable a gear ratio and allow for the relocation of the motor to allow for a larger, more powerful motor a belt drive is most suitable, similarly summarised in matrix xx where it can be seen that due to its reduced noise, maintenance frequency and cost as well as better manufacturability that

a belt drive is a more suitable than using a chain.

It was decided to use a high torque belt as can be seen in the profile xx, which allows for transmission of a large amounts of power xx, as well as high torque at a typical xx% efficiency as quoted by the manufacturer xx.

This style of belt is resistant to holding its shape after being held in a particular position, during storage, which would otherwise cause vibrations through the board. The flexibility from having teeth also helps negate this effect. Having teeth eliminates slip, which not only increases the efficiency but also reduces the heating of the pulleys. This is further decreased by the surface area of the teeth allowing for better heat transfer from a pulley to the belt and from the belt to air. The materials for the belt need to be able to withstand UV light so as not to degrade as the belt will be exposed to sunlight for prolonged periods of time. The chosen belt consists of a chloroprene compound combined with fibreglass tensile cords: chloroprene provides resistance to heating and a high shear tooth resistance, with the fibreglass cords allowing the belt to withstand the required torque without either snapping or stretching and thus reducing transmission efficiency. Additionally, the teeth are coated in a nylon covering, enhancing the belts durability and wear resistance.

The most appropriate method for mounting the motors is to attach them to the trucks as this ensures that the motors stay in the same relative position to the wheels during skateboard steering and providing constant tension in the transmission belt.

RISK ASSESSMENT

In order to eliminate road gravel from becoming trapped between the belt and the pulley and potentially locking up a pulley a casing was designed to protect the drive system as seen in xx. The main considerations of this case were:

- To keep dirt and gravel out
- To enable easy disassembly to clean out the inside from small particles that could possibly enter- ideally without the need for any tools so the user can perform this operation when on a ride.
- To be lightweight and add limited parts and manufacturing cost to overall design.

This system was designed in SOLIDWORKS xx and during initial manufacturing will be 3D printed using xx ABS xx ASA xx plastic due its high durability, impact resistance and (UV protection). If the production volume is increase at a future date the manufacturing of this part could be transitioned to be injection moulding alongside the production of the main battery and Vesc casing.

WHEELS

The wheels of the board constitute a vital component of the drive system, as they serve as the means of transferring power to the road and enabling motion. There are various factors here which can be optimised, such as power transfer maximisation for the driven wheels and running efficiency for the non-driven. The bearings have a significant effect upon the latter as they are key in the reduction of rolling resistance, making the choice of bearings a major design consideration. The final design consideration relating to the wheels concerns the connection between them and the power train. As a rear-wheel belt system was judged the most optimal, the task at this stage becomes determining the best manner of interfacing the belt with the rear wheels. Regarding the dimensions of the wheels, it was decided that as this design is a retrofit, the original wheel diameter of 70mm would be maintained. As this fall within the typical range for longboard wheels (60-100mm), this enables the torque values of the drive train to be compatible with a range of pre-existing boards.

WHEEL MATERIALS

The two sets of wheels (driven and non-driven) have significantly different roles: the driven set are required to propel the board, and as such must be of a material of sufficient traction to develop power at the road surface whilst being sufficiently resistant to abrasion to withstand extensive use without wearing out. In contrast, the non-driven wheels serve only to provide steering and low resistance to motion. Typical longboard wheels are made from polyurethane, which provides a μrolling in the range of 0.02-0.04 and a μstatic of 0.2. These values make polyurethane ideal for use in the non-driven wheels, with the small μrolling inducing low resistance with μstatic being large enough to provide enough traction for steering purposes. However, μstatic for polyurethane is insufficient to prevent slip should this material be used in the driven wheels. Rubber compounds provide a μstatic in the range 0.35-0.45, a significant improvement. However, natural rubber suffers from reduced abrasion resistance compared to polyurethane, thus synthetic rubbers are required: styrene butadiene (commonly used in car tyres) provided the ideal solution, enabling both the increased traction and wear-resistance required. Though this compound is more expensive than natural rubber, the wheels overall constitute a very small proportion of the overall material costs, thus the extra expenditure was deemed acceptable.

BEARINGS

Another essential consideration is the type of bearings to be used – the main criteria here are to maximise running efficiency by incurring as little rolling resistance as possible, whilst maintaining sufficient durability both in terms of long-term usage and resistance to sudden impacts. Three materials are widely used in skateboard bearings: steel, titanium and ceramic. Ceramics feature prominently in high-performance conventional skateboards due to their significant advantage in terms of rolling resistance over titanium and steel. This is due to such ceramics (most commonly Silicon Nitride) being about 640% harder than their metal counterparts, reducing deformation and thus energy loss. Additionally, silicon nitride has a high specific heat capacity (0.673kJ/kg), enabling continued performance at high speeds at which substantial heating is incurred. Ceramics also possess greater resistance to oxidation when exposed to moisture, allowing for long term durability without regular oiling. However, ceramics are prohibitively expensive, costing upwards of 360% more than steel and titanium. Additionally, ceramics are quite brittle materials, with yield and ultimate tensile strengths substantially lesser than metal bearings. The σUTS of 170MPa was deemed insufficient given the potential for high-speed impact that the board could suffer, making ceramics unsuited to the user case. In terms of rolling resistance, titanium (ASTM Grade 7) and steel (SAE52100) perform similarly, both exhibiting a Brinell Hardness of 200kg/mm2. SAE52100 has a slightly greater σUTS of 590MPa compared to 550MPa for titanium, which in combination with being the most affordable (£15/set) suggests that these would be the most advantageous material. However, with a heat capacity of only 0.475 kJ/kg, steel bearings are less suited to continued use at the high speeds the board will be capable of running at, and would require regular replacement due to the accelerated wear. Titanium however is more resilient to heating at 0.554 kJ/kg, resolving this issue, as well as being more resistant to oxidation. Though titanium is more costly at £25/set, this extra expenditure constitutes only a 1.1% increase in the overall cost of the board, indicating that titanium is the optimal choice as various design problems are resolved at minimal extra expense.

DRIVE TRAIN INTERFACE

The interface between the driving belt and the driven wheels is a major consideration within this design. As described above, a rear-wheel, belt-drive system was found to be optimal, and thus the design task became how to effectively connect the belt to the rear wheels. One option would have been to utilise an axle connecting both rear wheels, with the belts connected directly to this axle – this would have allowed for a simple integration of the belt with the driven wheels without the need to mount any components to the wheels directly. However, it would have required a radical redesign and implementation of non-standard trucks, as conventional designs that most boards are compatible with have both wheels mounted independently of each other, with no central axle. This problem was circumvented by opting to mount cogs directly to the rear wheels over which the toothed belt would run, additionally improving efficiency by removing any slip that may have occurred at the axle. Initially, a combination of mechanical and chemical fastenings was considered, such as screws combined with an adhesive. In keeping with common mechanical design practice, a factor of safety of at least 2 was deemed acceptable. Upon researching some of the market leaders in rubber-metal adhesives, it became clear that mechanical fixings would be unnecessary: the required tensile strength was estimated to be 0.15MPa, with all the adhesives considered being capable of such a load with wide factor of safety margins. With even the lowest costing adhesive achieving greater than 2 it was decided that the choice of adhesive could be based solely upon expense, as the higher FOS’ provided by the more costly glues (the highest at 141) were simply not required. The selected glue, Weicon GMK 2410 Rubber Metal Contact Adhesive, provides a factor of safety of 3.6 with the material cost running to less than 10 pence per wheel, meeting all design requirements for this component.

The finalised wheel design consists of two sets of wheels - the front wheels made of polyurethane to provide steering capability whilst keeping rolling resistance as low as possible, with the rear wheels of SBR rubber to provide the traction for power transfer whilst retaining long-term durability. The rear wheels will interface with the drive train via directly mounted cogs, attached adhesively with Weicon GMK 2410 glue. Both sets will run over titanium bearings, which provide the best compromise between running efficiency and resistance to wear, impact and heating.

TRUCKS AND SUSPENSION

Due to the need to mount motors to the trucks, it was clear that a new set of trucks would be required over the standard set that came in conjunction with the Mindless Longboard we were provided with as a prototype starting point. Initially, we considered designing our own custom trucks in-house in order to easily mount the motors whilst achieving the required load capacity and ground clearance. However, such a task would have taken up considerable resources and design time, and market research revealed that a wide array of commercially produced solutions was available – thus, it was decided to implement an off-shelf-solution and utilise the extra time and resources furthering the development of the more complex areas of the project. If the project were to be scaled up to mass-manufacturing, it would be worth reconsidering as designing and producing our own trucks could potentially reduce overheads and would also reduce our reliance on external partners, decreasing the risk of the overall business model. However, for this one-off prototype, the commercial solution remains the best option.

FINAL IMPLEMENTATION

After considerable market research, a set of trucks and motor mount from Torque Motors were selected. The trucks possess a track width of 218mm (314mm w/ axles) and are compatible with the corresponding V6 motor mount. This mount is suited for supporting two motors and has length of 63mm, enabling the use of the 6374 motors required by the drivetrain. The trucks have a light all-aluminium construction, giving them a mass of 0.55kg each (1.1kg front and rear) – this was considered acceptably small as it would constitute less than 1% of the specified rider’s bodyweight and thus have little affect on the board’s performance.

LIMITATIONS

One major drawback of this solution is that these trucks do not incorporate any form of suspension. Initially, we had deemed suspension to be a desirable component in order to improve ride quality; however, the majority of commercially available trucks on the market do not cater to this requirement, with those that do being additionally heavy, prohibitively expensive and requiring a high level of maintenance. Such suspension systems are commonly used in off-road and stunt-style skateboarding, which makes for an unrealistic comparison for our urban-based user case. As trying to incorporate this feature into the design would hinder not only the performance of the board due to the increased weight, but also reduce its marketability due to the extra expense, this limitation with regards to suspension was considered acceptable as the suspension was of lesser importance to satisfying the user case than other areas of the design that could benefit from the time and resources.

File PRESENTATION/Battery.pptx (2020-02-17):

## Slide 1

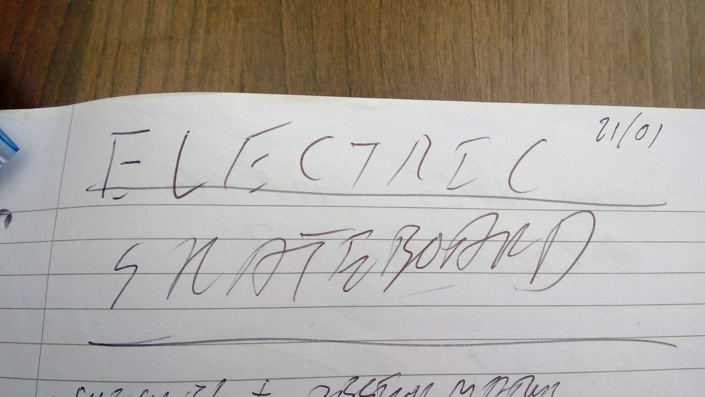
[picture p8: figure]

## Into - toby

## BOARD - ED

## TRUCKS - TOBY

## Wheels - HUGO

## Battery – SAM

## Range specification

Specification
- Charge every week: 7 days
- Days in use: 5 days (commute)
- Distance each day: 3km
- Estimated vertical distance: 80m
This means:
- Estimated Watt-hours per mile: 10Wh/mile

## Battery specification

Lithium polymer chemistry
- Watt-hour capacity: 180Wh
- Supply voltage:22.2V
- Amp-hour capacity: 8100Ah
- Mass: 1.7kg
- Supply voltage: 50v
- 2 batteries in parallel required


## Battery charging

- Lithium polymer can be dangerous:
  - Overcharging
  - Unbalanced charging
- Use an off the shelf solution
- Use hobby/RC charger
- Charge batteries in parallel
- System to switch between series and parallel

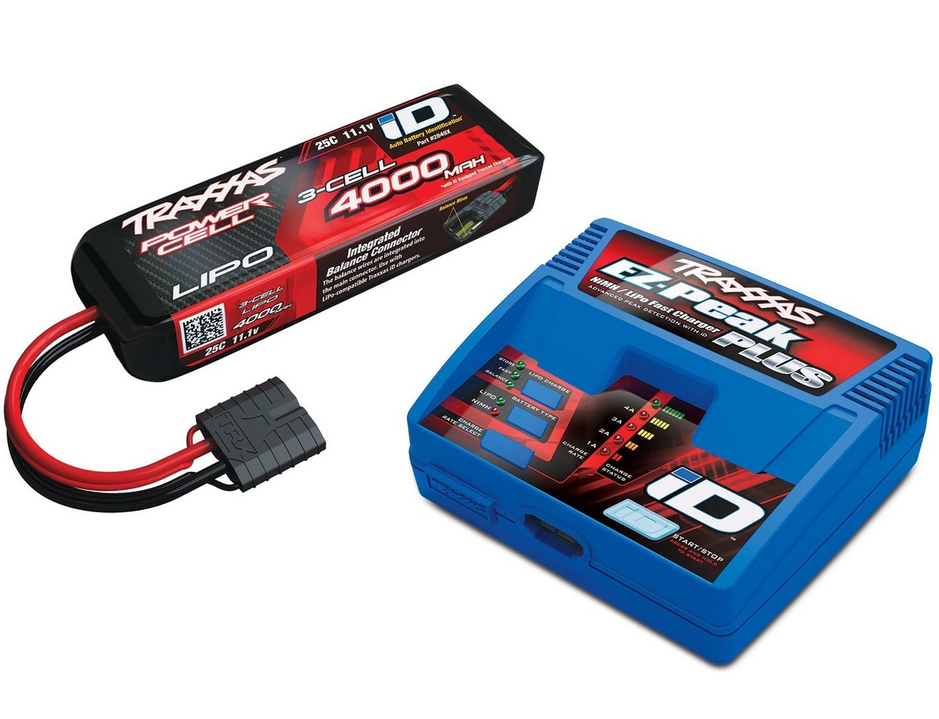
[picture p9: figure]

## Battery control overview

## Battery embedded controller

- STM8L – microcontroller
- Ultra low power 10 μA sleep state
- Separate battery supply
- Monitors battery health
  - Volts
  - Time
  - Cycle count
- Controls battery mux
- Controls charge circuit
- Heartbeat signal from main micro

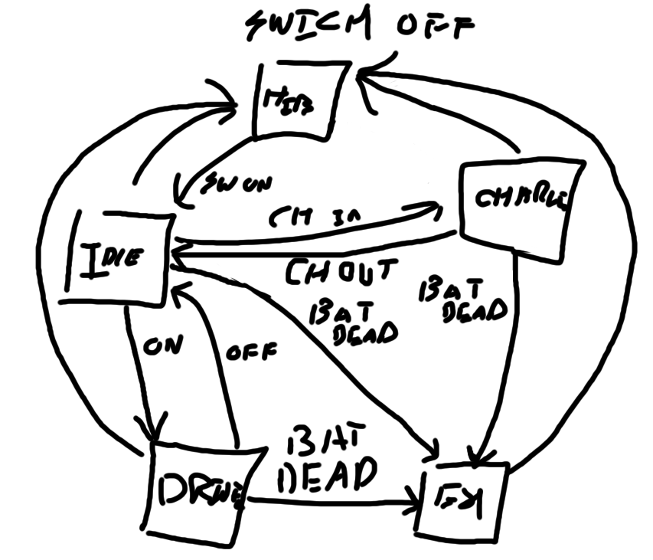
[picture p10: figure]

## Battery error state

- LED binary error code report
- Flashes on when power button is hit
- Lookup table in manual

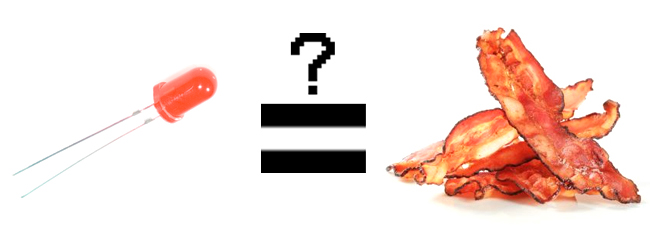
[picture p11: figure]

## Battery mux

- Two large batteries
States:
  - Charge in parallel
  - Discharge in series
- Electrically controlled path switching
- Vibration resistant
- Short resistant
- Bidirectional current flow (balanced charging)

## Switching technology

Relay:
- Mechanical switch
- Very High voltage
- Very High current
- Low standby draw

Bipolar power switch(BPS):
Solid state system
MOSFET switching
Higher power dissipation
Fast switching

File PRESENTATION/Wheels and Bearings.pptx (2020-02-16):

## Wheels and Bearings

## Wheel Materials

Polyurethane
- μ-rolling = 0.02-0.04 Acceptable for non-driven
- μ-static = 0.2 Insufficient for driven
Rubber
- μ-static = 0.35-45 75-125% Improvement

## Bearing Materials

Material | σUTS (MPa) | Brinell Hardness (kg/mm²) | Approximate Cost (£)
Steel: SAE-AISI 52100 | 590-2100 | 180-210 | 15
Titanium: ASTM Grades 7 | 550 | 200 | 25
Ceramic: Silicon Nitride | 170 | 1479 (converted from Vickers’ hardness) | 70-115

Steel and Titanium perform similarly
Titanium favoured due to greater wear and corrosion resistance despite greater cost

## Wheel-Gear Adhesives

Estimated Minimum Tensile Strength Required σ_T ~0.15N/mm^2

Adhesive | Tensile Strength (N/mm²) | FOS | Cost (£/gram) | Cost(£/mm²) | Cost (per wheel)
Weicon GMK 2410 Rubber Metal Contact Adhesive | 0.54 (Steel to SBR Rubber) | 3.6 | 0.124 | 3.72x10^-5 | 0.0954
Cole-Parmer Silicone Rubber Bonding Cement: DOWSIL™ 732 Multi-Purpose Sealant | 2.3 | 15.3 | 0.1367 | 4.101x10^-5 | 0.1052
Loctite Super Glue ULTRA Gel Control | 21.12 (Aluminium to Rubber) | 140.8 | 1.623 | 4.869x10^-4 | 1.249

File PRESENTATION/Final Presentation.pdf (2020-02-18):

# L2AHTB1: Electric Skateboard

### P.M. Toby Ashton, Jacob Black, Haydn Lisk, Hugo McCartney, Edward Street, Sam Sutcliffe

# Introduction

## - Retrofit for wide range of available boards - Commuting and recreation - Predicted Load: 120kg - High performance - Maximum Range: 15km - Top Speed: 15m/s on flat, 8m/s on max gradient - Weight: 8kg

# Board

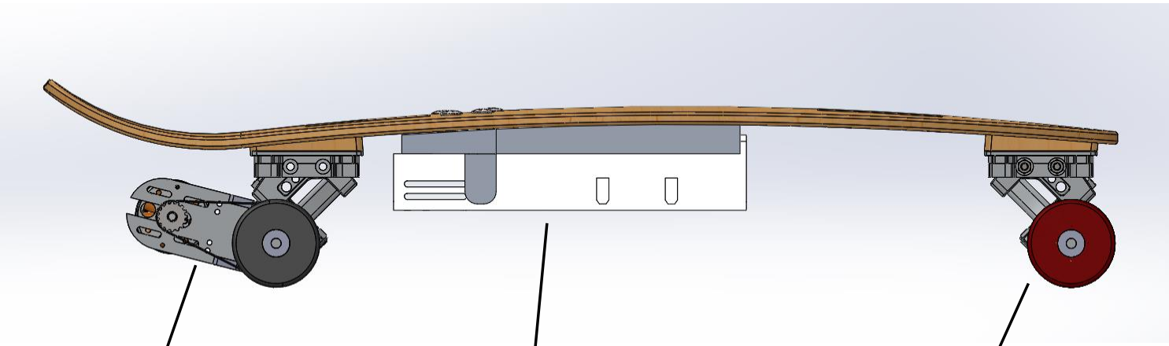
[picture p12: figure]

Rear Trucks with integrated
motor and drivetrain | Electrical components
| casing

Symmetrical front trucks

# Board Analysis

Stress Analysis
FEM analysis
- 120kg user load concentrated at centre
- Approx. 4.5kg components
- High stress at truck fixtures and center of board
- 35.9MPa maximum compressive stress
- Does not exceed compressive yield stress

Displacement Analysis
- 4.6mm maximum deflection

# Electronic Components

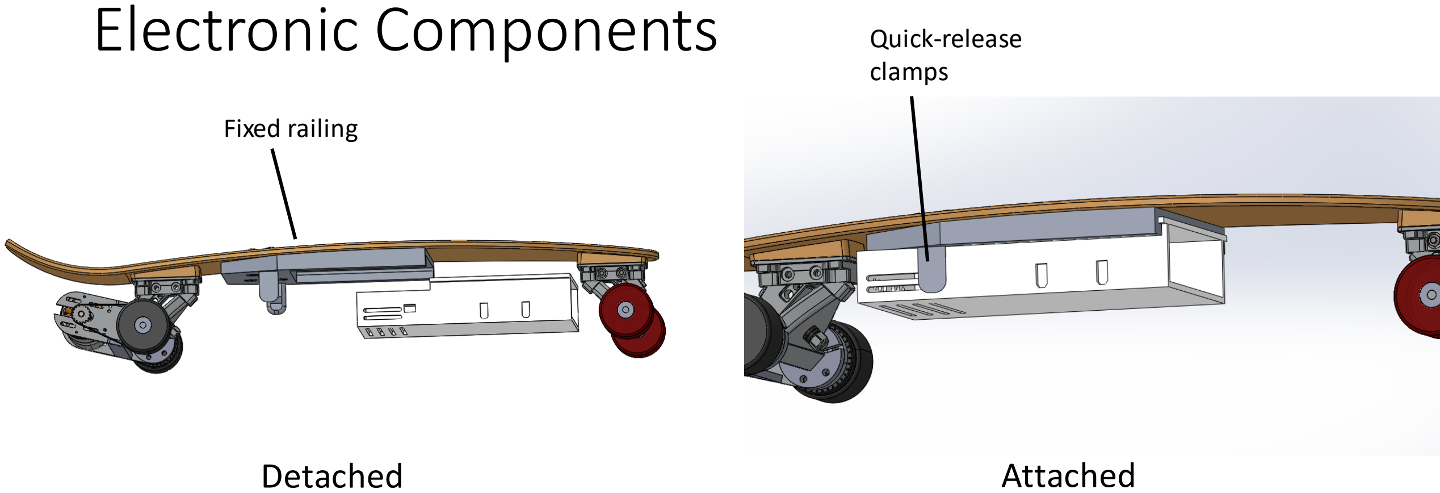
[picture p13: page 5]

Detached | Attached

Quick-release
clamps

Fixed railing

# Battery Box

Control Electronics:
ESC, Microcontroller
Batteries | Ventilation Slots

Charging Port

Motor
connections

# Material Selection

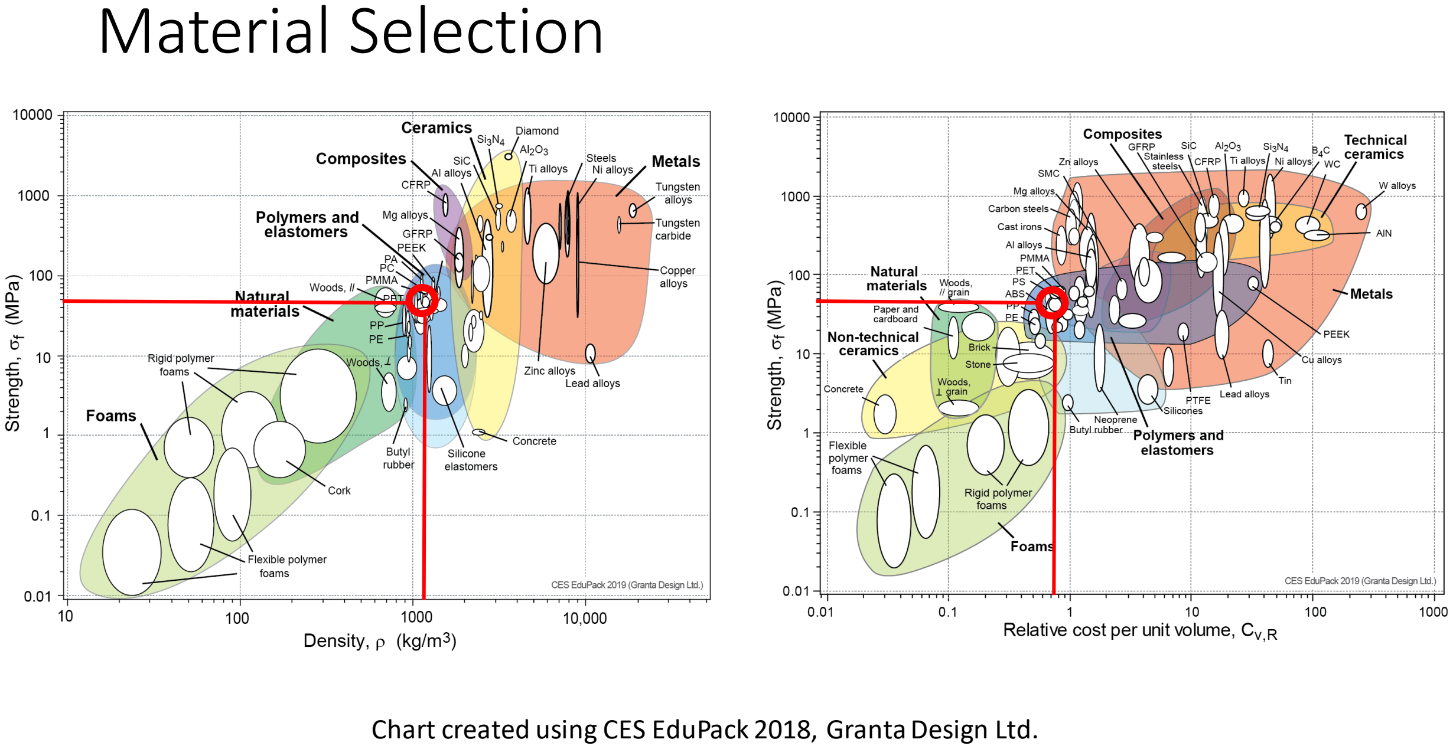
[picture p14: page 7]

Chart created using CES EduPack 2018, Granta Design Ltd.

# Battery Box

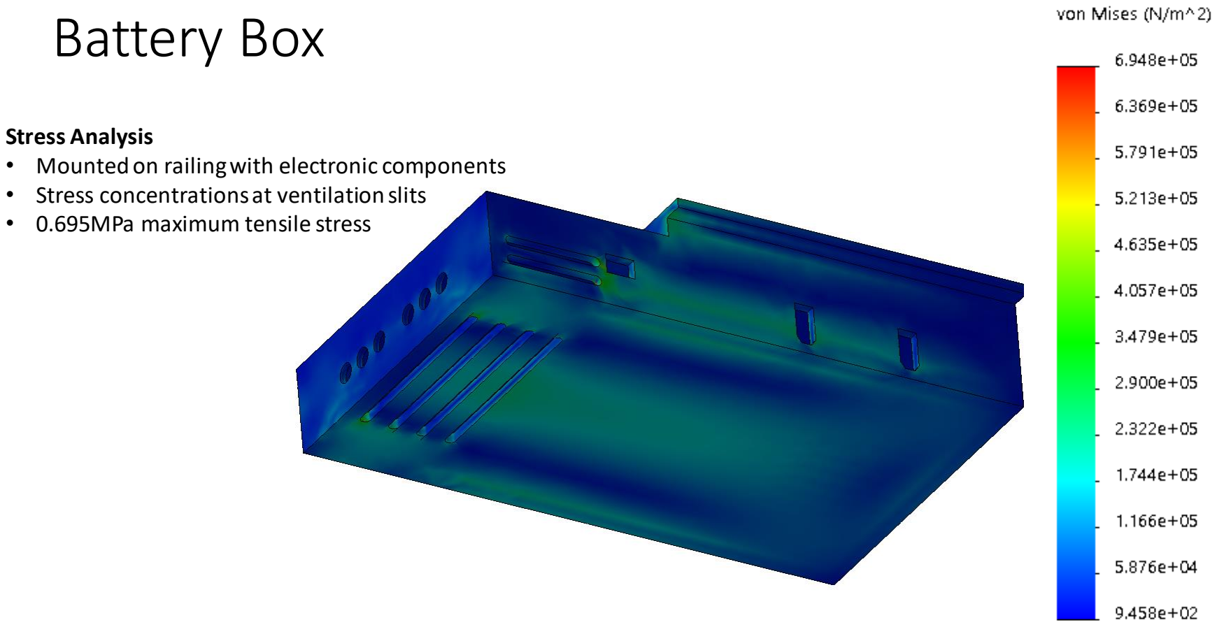
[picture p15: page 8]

Stress Analysis
- Mounted on railing with electronic components
- Stress concentrations at ventilation slits
- 0.695MPa maximum tensile stress

# Railing

Stress Analysis
- Attatched battery
- Stress concentration at inner corners
- 0.987MPa maximum compressive stress

Displacement Analysis
- Approx. 0.46mm maximum deflection
- Total ground clearance = 6.5 cm when loaded

# Trucks

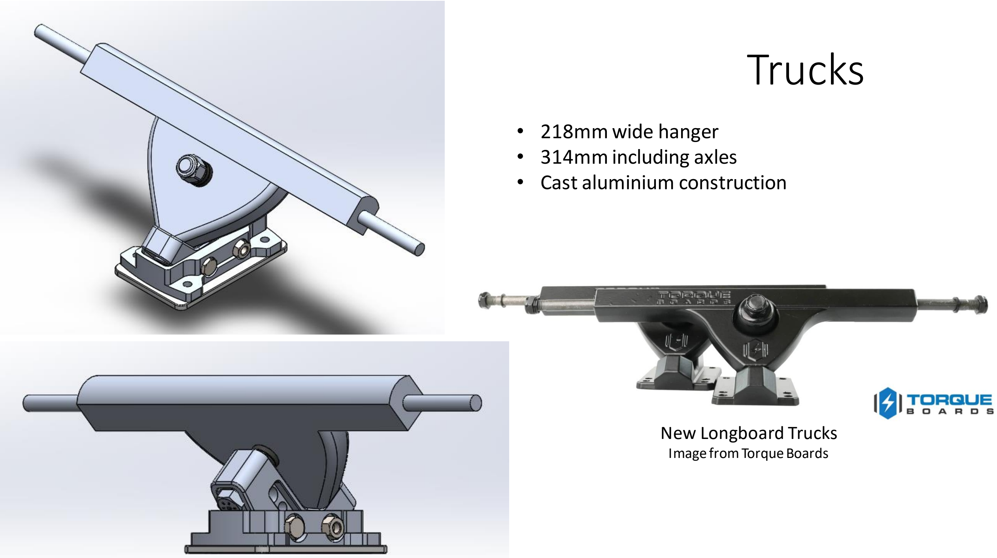
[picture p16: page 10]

- 218mm wide hanger
- 314mm including axles
- Cast aluminium construction

New Longboard Trucks
Image from Torque Boards

# Motor Mount

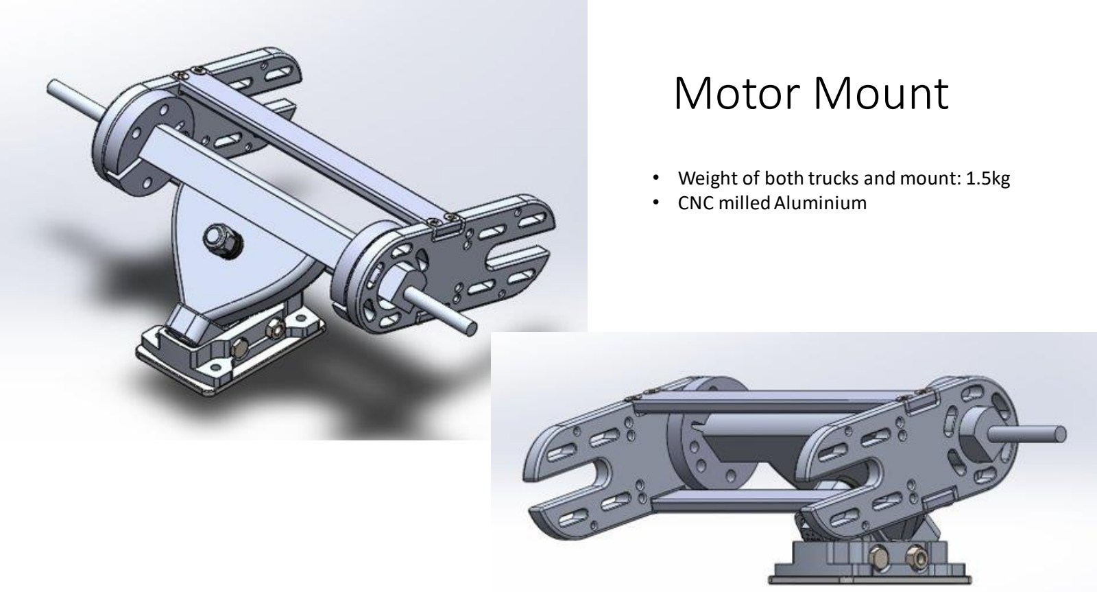
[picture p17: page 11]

- Weight of both trucks and mount: 1.5kg
- CNC milled Aluminium

# Wheels

- Wheel Dimensions
- Wheel Materials
- Bearing Materials
- Wheel-Gear Attachment

# Wheel Materials

Material | μ-rolling | μ-static | Cost (£/wheel)
Polyurethane | 0.02-0.04 | 0.2 | 2.50-37.50
Rubber | 0.02-0.04 | 0.35-0.45 | 3.80
Conclusion | Both acceptable for non-driven | Rubber provides 75-125% in μ-static, better for driven wheel | Greater variation in polyurethane, customer's preference

# Bearing Materials

Material | σUTS (MPa) | Brinell Hardness (kg/mm² ) | Specific Heat Capacity (kJ/kgK) | Approximate Cost (£)
Steel: SAE-AISI 52100 | 590-2100 | 180-210 | 0.475 | 15
Titanium: ASTM Grades 7 | 550 | 200 | 0.554 | 25
Ceramic: Silicon Nitride | 170 | 1479 (converted from Vickers’ hardness) | 0.673 | 70-115

# Wheel -Gear Adhesives

## Estimated Minimum Tensile Strength Required σ ~ 0.15N/mm^2

Adhesive | Tensile Strength (N/mm² ) | FOS | Cost (£/mm² ) | Cost (£/per wheel)
Weicon GMK 2410 Rubber Metal Contact Adhesive | 0.54 | 3.6 | 3.72x10^-5 | 0.0954
Cole-Parmer Silicone Rubber Bonding Cement: DOWSIL™ 732 Multi-Purpose Sealant | 2.3 | 15.3 | 4.101x10^-5 | 0.1052
Loctite Super Glue ULTRA Gel Control | 21.12 | 140.8 | 4.869x10^-4 | 1.249

# Drive System Configuration

Category | Weighting (/5) | FWD Belt | FWD (2x Hub) | RWD Belt | RWD (2x Hub) | AWD Belt | AWD (4x Hub)
Weight Distribution | 3 | 1 | 1 | 4 | 4 | 3 | 3
Handling | 3 | 3 | 3 | 3 | 3 | 4 | 4
Cost | 3 | 4 | 2 | 4 | 2 | 3 | 1
Manufacturability | 4 | 4 | 3 | 4 | 3 | 2 | 2
Safety | 4 | 4 | 4 | 4 | 4 | 5 | 5
Control Complexity | 4 | 4 | 2 | 4 | 2 | 3 | 2
Transmission Efficiency | 4 | 3 | 4 | 3 | 4 | 2 | 5
Total | | 84 | 70 | 93 | 79 | 78 | 80

# Drivetrain Requirements

## - High Torque - High Speed - Efficient Power Transmission - Quiet - Compact - Affordable

# Drivetrain Types

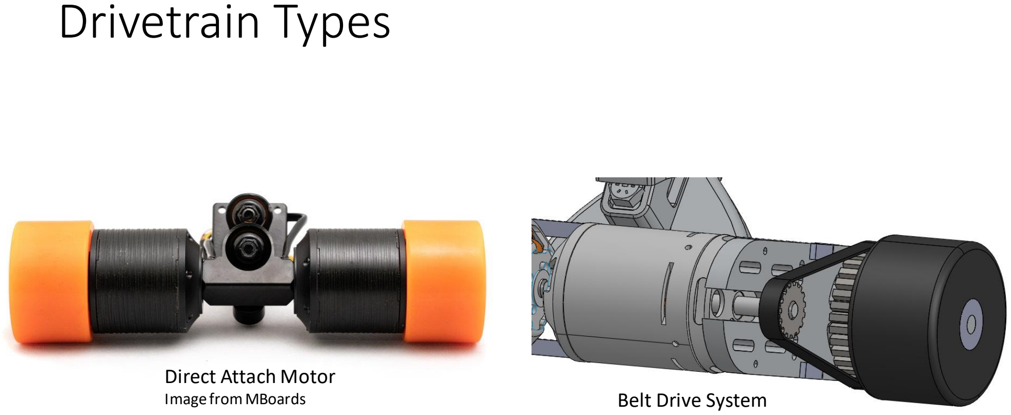
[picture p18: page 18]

Direct Attach Motor
Image from MBoards | Belt Drive System

# Types of Belt

Image from gpr industrial

Conventional Timing Belt
Image from Megadyne

High Torque Belt
Image from Megadyne

High Torque
Motor/ Wheel Pulley
Image frombelting online

# Motor

AC Induction | Efficient Quiet Hard to control High torque at startup
DC Brushed | Easy Control Inefficient High Speed
DC Brushless | Easy Maintenance Long Lifespan Easy Control Efficient

# Drive Circuitry

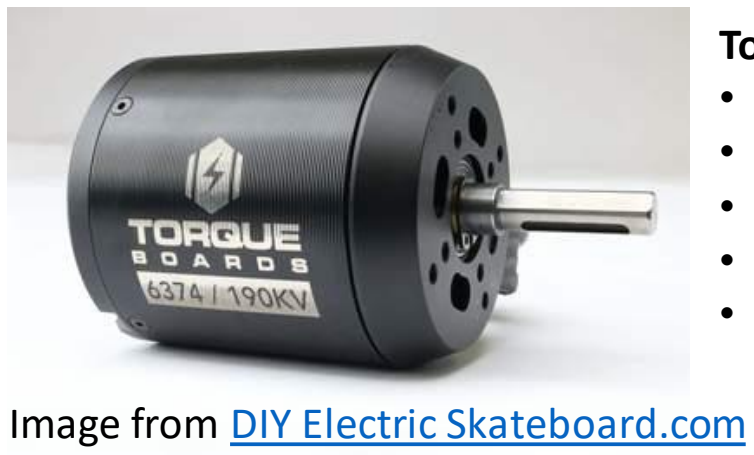
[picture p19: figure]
Image from DIY Electric Skateboard.com

Torque Boards 6374 190KV Motor:
- Maximum Current: 80A
- Maximum Voltage: 12s (A 12 cell LiPo)
- Maximum Torque: 3.57 Nm
- Integrated Hall Effect sensor.
- Manufacturer Recommended ESC: 12S 120A Car ESC

12S 120A Car ESC:
- Continuous Current Rating: 120A
- Burst Current Rating: 1080A (10 sec max)
- Maximum Voltage: 12s
- Forward and reverse capability
- PWM Control

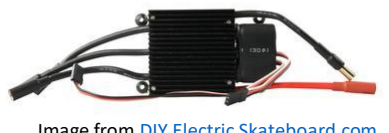
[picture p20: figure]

Image from DIY Electric Skateboard.com (https://diyelectricskateboard.com/products/torqueboards-12s-120a-car-esc-opto-hv)

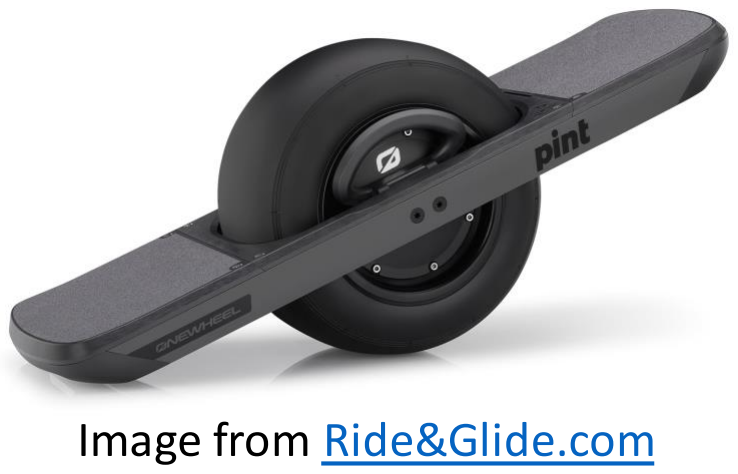
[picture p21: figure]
Image from Ride&Glide.com

# Pressure Pad Throttle Control

## - Already an existing technology, used on OneWheel - Measures the weight distribution of the rider - Lean forward accelerates, lean back decelerates - Less complex to develop than the handheld wireless remote used by Boosted - Can detect rider dismount (stop the board)

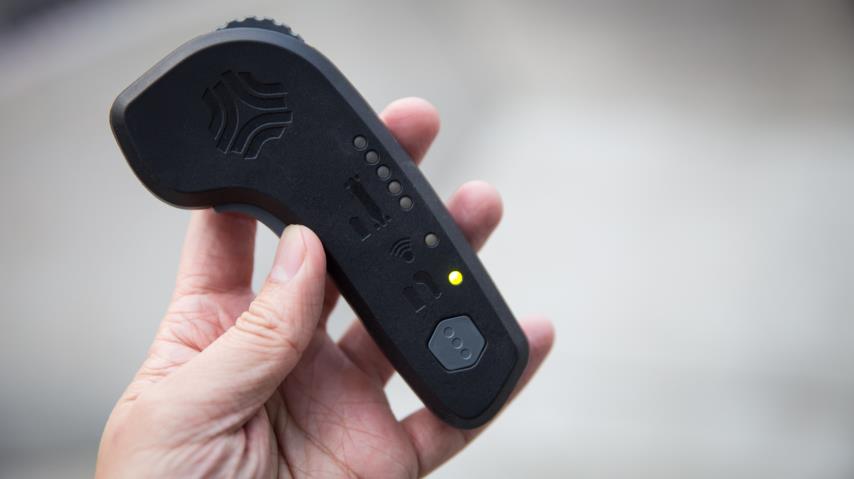
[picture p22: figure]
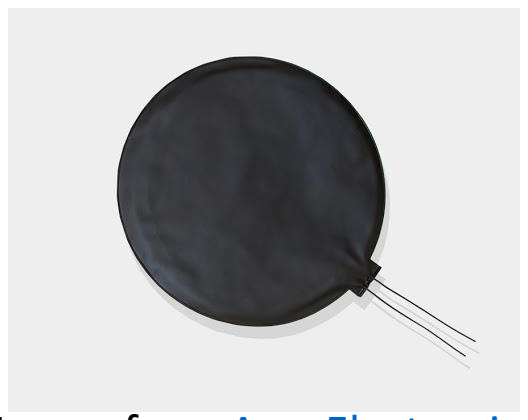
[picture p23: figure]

Image from ArunElectronics (http://www.arun-electronics.co.uk/pressure_mat.htm) | Image from Tested.com (https://www.tested.com/tech/469363-testing-boosted-boards-electric-longboard/)

# Microcontroller

## - Need a system to provide PWM signals to ESCs

## - Maps the throttle input to an acceleration of the motors - Power supply – regulated supply from battery - LCD monitor – debugging and status

# Block Diagram

- 50v Supply Rail
- 5v Rectified Supply Rail

# Block Diagram

ESC and Motor Module:
- 2 Pairs
- Controlled by PWM Signal
- Hall Effect Sensors to measure rotation speed

# Block Diagram

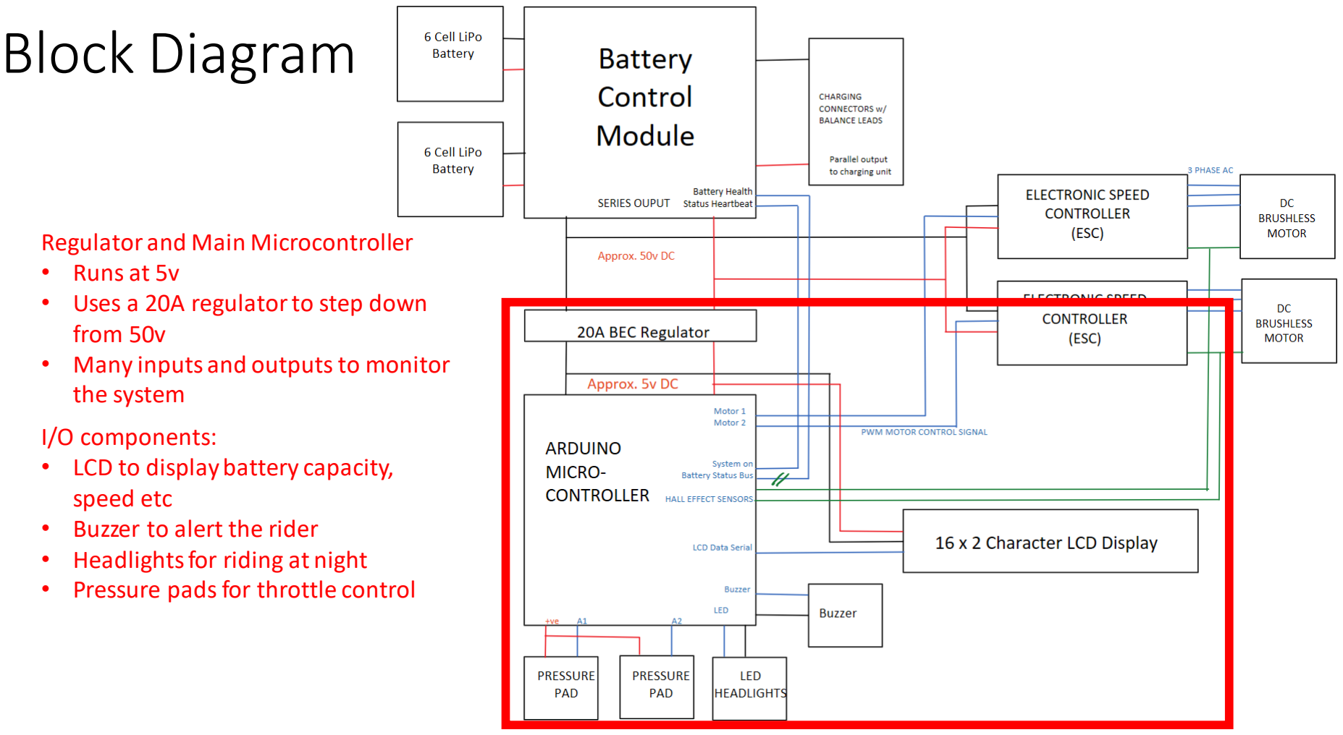
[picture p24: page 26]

I/O components:
- LCD to display battery capacity, speed etc
- Buzzer to alert the rider
- Headlights for riding at night
- Pressure pads for throttle control

Regulator and Main Microcontroller
- Runs at 5v
- Uses a 20A regulator to step down from 50v
- Many inputs and outputs to monitor the system


## - Calibration Stage - Main loops sends heartbeat periodically - Checks for system safety, stopping drive if it falls outside safe bounds - Reads pressure pads to find the acceleration - Sends signals to ESCs - Displays system status to user on LCD

# Block Diagram


Battery Control Module:
- Receives a heartbeat from Main Microcontroller
- Reports back battery status to Main Microcontroller

# Range specification

## Specification - Charge once per week - Days in use: 5 days (commute) - Distance each day: 3km - Estimated vertical distance: 80m

## - Range on full charge: ~15km - Estimated energy per mile: 10Wh/mile


- Min capacity requirement: ~180Wh | Google maps example commute

# Battery specification

## Lithium polymer chemistry - Watt-hour capacity: 180Wh - Supply voltage:22.2V - Amp-hour capacity: 8100mAh - Mass: 1.24kg

## - Supply voltage: 50v - 2 batteries in series required


Figure from Comparison of Energy Density in Battery Cells- NASA (https://www.researchgate.net/figure/Comparison-of-Energy-Density-in-Battery-Cells-NASA-National-Aeronautics-and-Space_fig1_327237748)

# Battery charging

## - Lithium polymer can be dangerous:

## - Overcharging - Unbalanced charging

## - Use an off the shelf solution - Use hobby/RC charger

## - Charge batteries in parallel

- System to switch between series and parallel | https://traxxas.com/product
| s/parts/2994

## - Battery series/parallel multiplexer - Microcontroller - Independent power supply - Current monitors - Isolation switches - Fuses - Communication bus

# Battery control overview

# Battery multiplexer (mux)

## - Two large batteries States:

## - Charge in parallel - Discharge in series - Disconnected

## - Electrically controlled path switching - Vibration resistant - Short resistant

## - Bidirectional current flow (balanced charging)

# Multiplexer (cont)


## - Discharge

## Equivalent circuit

# Multiplexer (cont)


## - Charge

## Equivalent circuit


# Multiplexer (cont)

## - Charging - Balance leads in parallel - Connects to charger

# Switching technology

## Relay: - Electro-Mechanical switch - Very high voltage - Very high current - Low standby draw

## MOSFET power switch: - Solid state system - Low current - Higher power dissipation - Extra drive circuitry


## Stock images from Farnell

# Battery embedded controller


## - STM8L – microcontroller - Ultra low power 10 μA sleep state - Separate battery supply - Monitors battery health

## - Volts - Time - Cycle count

## - Controls battery mux - Heartbeat signal from main micro

# Safety Measures

## - Conducted a Failure Mode Analysis - Determines edge cases which could lead to system damage/failure - Plans mitigation factors


# Servicing

## - Lithium battery take back scheme & disposal - Replace main batteries and coin battery - Test and maintain circuitry - Check mechanical parts for damage - Replace consumable parts

# End of Life

## - Lithium Polymers

## - EEE Waste - Readily removeable - Labelled fully

## - ABS plastic and wood are easily recyclable - Metal can be scrapped

Image from GOV.uk

# Costing

## - Material Costs: £880

## - Boosted Boards 'Boosted Plus'

## - Retail Price: £1300

## - OneWheel's 'XR'

## - Retail Price: £1400

Cost (£) | Item

£50.00 Front and Rear Trucks (Torque Motors)

£72.00 Motor Mount (Torque Motors 'V6')

£7.74 | Rubber Driven Wheels (x2)

£12.98 Titanium Bearings (x4)

£0.19 | Weicon GMK 2410 Rubber Metal Contact Adhesive
£184.00 | 6374 DC Brushless Motors (x2)

£20.60 36 Tooth HTD5 Cog (36-5M-09F) (x2)

£5.98 | 12 Tooth HTD5 9mm Motor Cog (x2)

£21.48 Belt HTD 300-5M-9 Continental (x2)

£126.00 | Li-Po Battery (x2)
£0.67 | Coin battery CR2032
£5.00 | Switch driver LTC7004

£38.00 Battery charger

£13.50 Power switches FDC6324L (x30)

£1.50 | Low power micro STM8L 152C6T6

£30.00 Box and Rail ABS cost

£220.00 | ESC (x2)

£70.00 Miscellaneous Parts

£879.64

# Questions

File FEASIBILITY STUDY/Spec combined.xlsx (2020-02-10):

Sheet: User specification
User specification
Fast enough to use on roads
Can handle expected hill graidents
Not loud
Typical usage range (single charge)
Max charge time
Maintainence lifespan
Max weight
Min charge time | 90 mins

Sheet: Techincal specification
Techinical specification
Drive train:
Maximum gradient | 10 deg
Maximum speed flat | 15ms-1
Maximum speed uphill | 8ms-1
Maximum noise- quiet under full load, drowned out by typical car traffic | 70dB
Minimum Motor power | 2000w
Battery:
Charge time period - 1/f | 7 days
Max charge rate (C rating) | 1C
Minimum amp-hour supply
Cycle life required | 500 cycles | FS 2
Power supply rail voltage | 50V | 12S
Minimum capacity | 180Wh | 100%DOD
Battery mass maximum | 5kg
Depth of discharge | 90%
FoS cycle life | 2
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

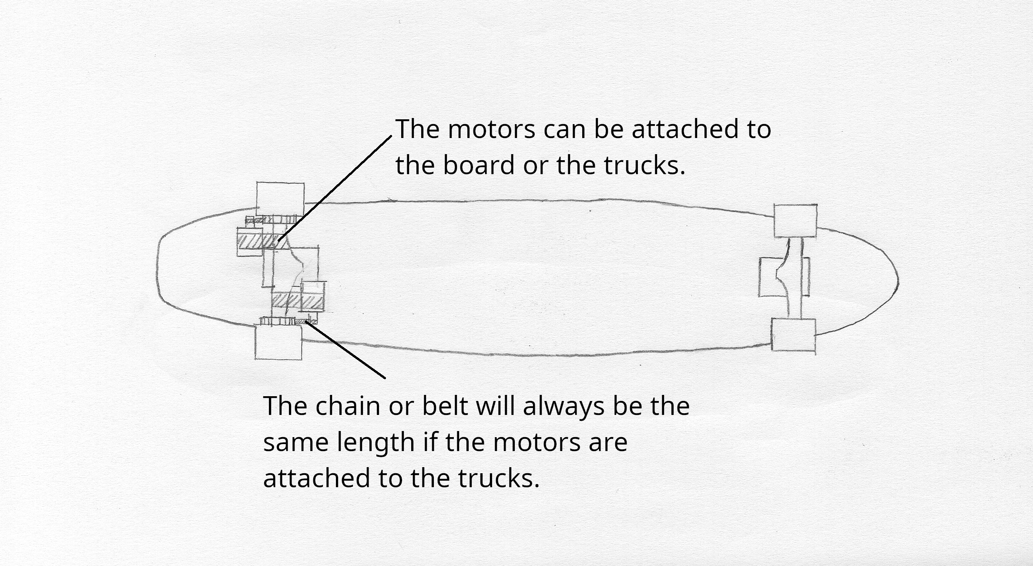
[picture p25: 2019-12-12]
FEASIBILITY STUDY/Drivetrain/Images/Drivetrain3Lab.png

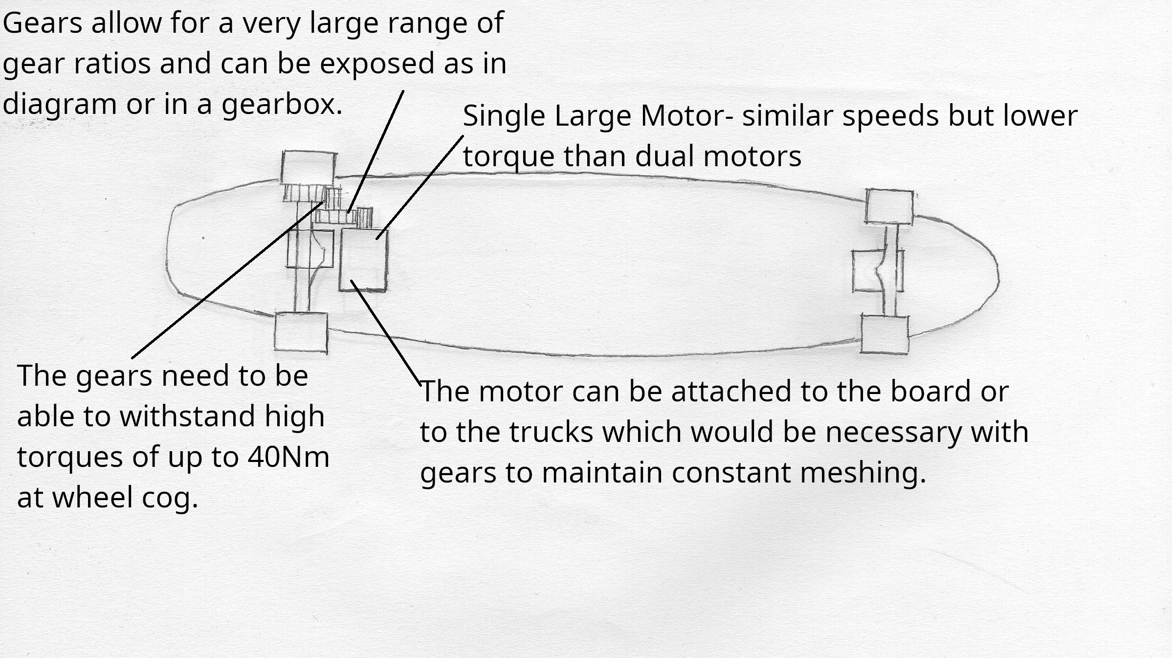
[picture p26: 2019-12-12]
FEASIBILITY STUDY/Drivetrain/Images/Drivetrain1Lab.png

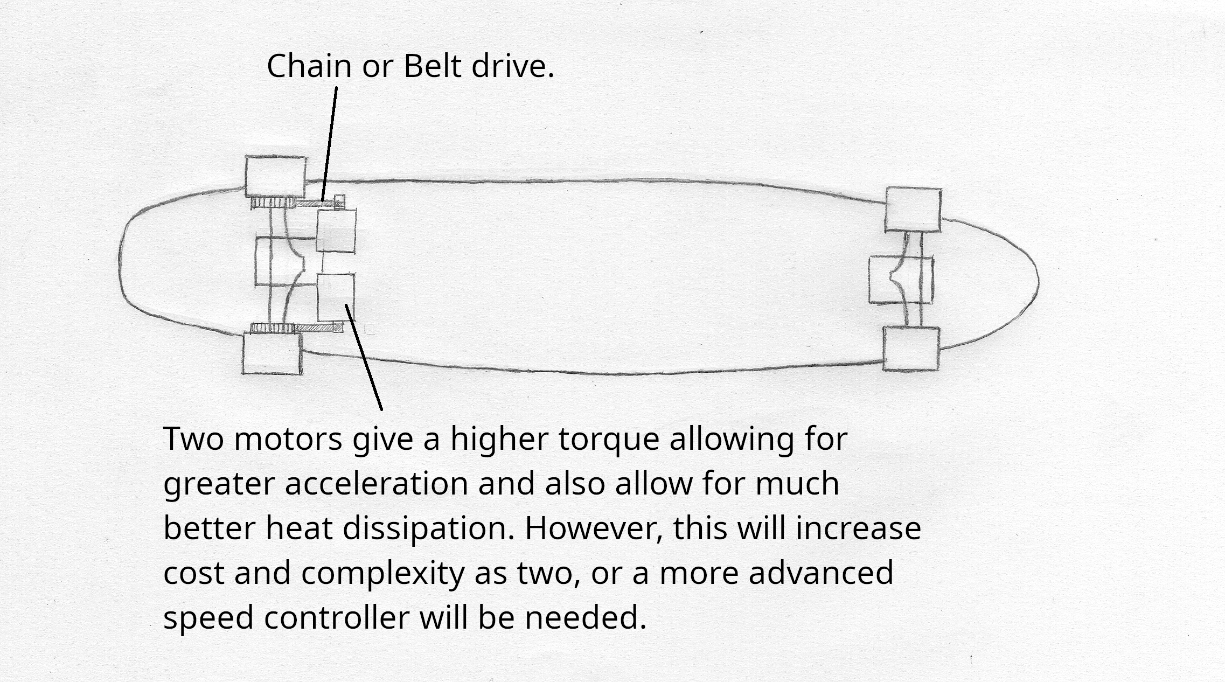
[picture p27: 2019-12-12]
FEASIBILITY STUDY/Drivetrain/Images/Drivetrain2Lab.png

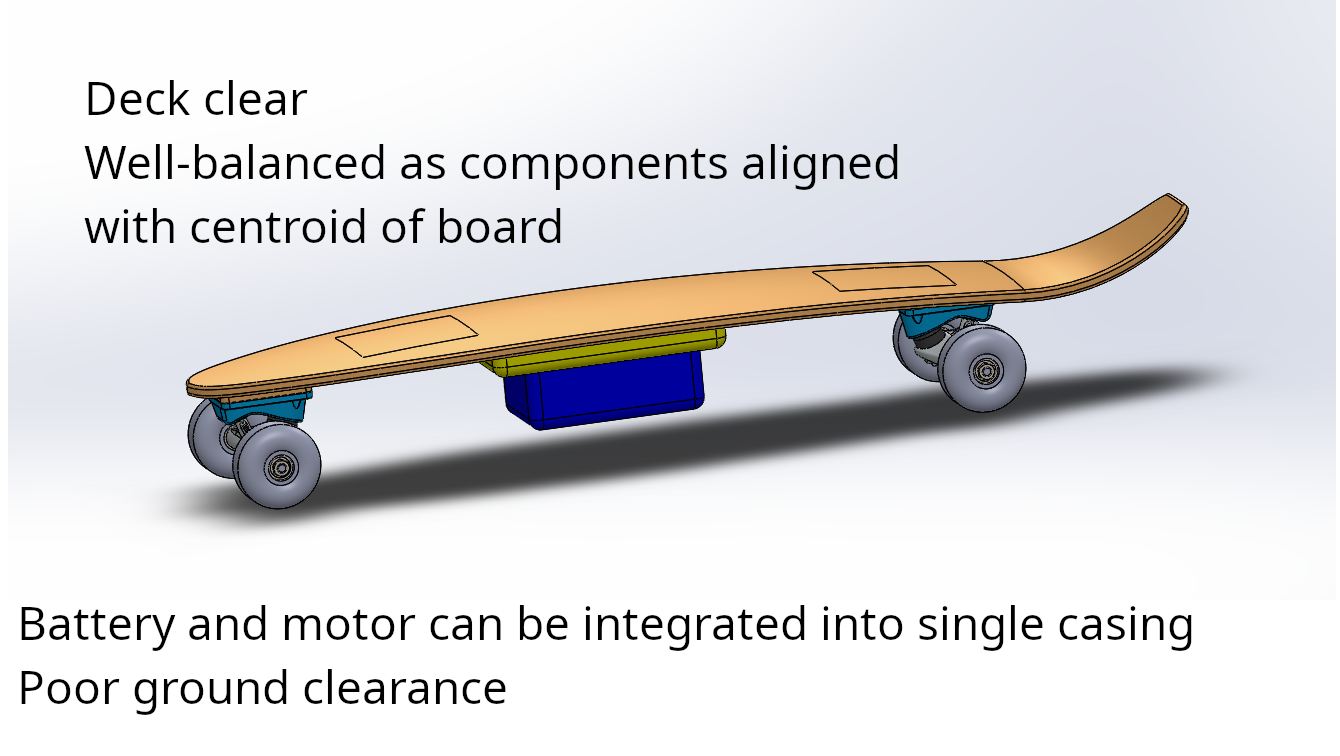
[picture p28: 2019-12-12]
FEASIBILITY STUDY/Board/Concept_E.png

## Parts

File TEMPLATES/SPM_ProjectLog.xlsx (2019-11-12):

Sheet: Project_Log
Activity Type | Activity Name | Activity Description / Comment | Submitted by | Submited Date | Status | Impact on Task | Impact on Budget | Impact on Schedule | Implemented by | Implement Date | Confirmed by | Confirm Date
Meeting Note | Agenda 10/10 | Goals & Objectives Postit note exercise | project.manager@university.org | 2018-10-11 | Done
Meeting Note | Agenda 17/10 | Complete project scope | project.manager@university.org | 2018-10-18 | Done
Meeting Note | Agenda 24/10 | First schedule draft | project.manager@university.org | 2018-10-25 | Done
Meeting Note | Meeting 01/11 | Meeting: entire team, two project sponsors | project.manager@university.org | 2017-11-01 | Done
Meeting action | Meeting 01/11 | Revise plan with activities no more than 20% of the total budget | project.manager@university.org | 2017-11-01 | Done |  |  |  | project.manager@university.org | 2018-11-05 | DirectorToBeNamed@university.org | 2018-11-05
Meeting action | Meeting 08/11 | Add to select Power button: "Volume +-" and "Prev<>Next" buttons | designer.engineer@university.org | 2017-11-08 | Open | Select Power Button | plus 5 days of work | 5 days delay
Reminder | Invite Pi distributor to the December meeting |  | software.engineer@university.org | 2017-11-10 | Discarded
Risk review | Monthly risk review Dec | No additional risks to the project | programmer.engineer@university.org | 2017-12-01 | Done
Scope change | Add touchscreen |  | electronics.engineer@university.org | 2017-12-01 | Discarded | Design Case Internals | + £40 | 4 days delay
Issue | Raspberry Pi price increase | It is expected that the next version of Raspberry Pi is 100% more expensive | project.manager@university.org | 2017-11-03 | In progress | Market Analysis | none | none
Meeting action | Contact customer | Setup a meeting to discuss the user testing of the prototype | programmer.engineer@university.org | 2018-11-05 | Scheduled

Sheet: Contacts
FirstName | FamilyName | Email | Organisation | Phone | Mobile | Address
Oliver | Vogt | oliver.vogt@university.org | EngineeringCompany
Designer | Engineer | designer.engineer@university.org | EngineeringCompany
Programmer | Engineer | programmer.engineer@university.org | EngineeringCompany
Manufacturing | Engineer | manufacturing.engineer@university.org | EngineeringCompany
Director | ToBeNamed | DirectorToBeNamed@university.org | EngineeringCompany
Marketing | ToBeNamed | MarketingToBeNamed@university.org | EngineeringCompany
Finance | ToBeNamed | FinanceToBeNamed@university.org | EngineeringCompany
Bank | ToBeNamed | BankToBeNamed@university.org | Lloyds Bank
S-Customer | standard | S-CustomerToBeNamed@university.org | Rapid Electonics
Adv-Customer | advanced | Adv-CustomerToBeNamed@university.org | Amazon
Retailer | ToBeNamed | RetailerToBeNamed@university.org | Carphone Warehouse
Wholesaler | ToBeNamed | WholesalerToBeNamed@university.org | Amazon
IT-Support | ToBeNamed | IT-SupportToBeNamed@university.org | Waterstone Consultancy
Design | Tutor1 | design.tutor1@university.org | Waterstone Consultancy
Design | Tutor2 | design.tutor2@university.org | Waterstone Consultancy
software | engineer | software.engineer@university.org | EngineeringCompany
electronics | engineer | electronics.engineer@university.org | EngineeringCompany
project | manager | project.manager@university.org | EngineeringCompany
Project | Sponsot | project.sponsor@company.com | Lloyds Bank

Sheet: DataValidation
Open
Scheduled
In progress
Done
Discarded

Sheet: Tasks
Deliverable | Task Name | Description | Who (Responsible) | Where | Comment
Case & Cables | Design Case Internals |  | designer.engineer@university.org
Case & Cables | Simulate Assembly |  | manufacturing.engineer@university.org
Case & Cables | Research Power Supply |  | manufacturing.engineer@university.org
Case & Cables | Design Case outside |  | designer.engineer@university.org
Case & Cables | Case Durability / FEA |  | manufacturing.engineer@university.org
Case & Cables | Research Raspberry Pi Alternatives |  | manufacturing.engineer@university.org
Case & Cables | Research Manufacturing Options |  | manufacturing.engineer@university.org
Loudspeaker | Select Loudspeaker |  | electronics.engineer@university.org
Loudspeaker | Market Analysis |  | electronics.engineer@university.org
Market Analysis | Carry out competitor analysis |  | project.manager@university.org
Market Analysis | Carry out a customer analysis |  | project.manager@university.org
Power Supply | Select Power Supply |  | electronics.engineer@university.org
Power Supply | Select Power Button |  | electronics.engineer@university.org
Power Supply | Select Volume Button |  | electronics.engineer@university.org
Power Supply | Research Power Supply |  | software.engineer@university.org
Power Supply | Research Power Button |  | software.engineer@university.org
Power Supply | Research Volume Button |  | software.engineer@university.org
Program Pi | Evaluate App Options |  | software.engineer@university.org
Program Pi | Research Plattforms |  | software.engineer@university.org
Program Pi | Connect to Raspberry Pi |  | electronics.engineer@university.org
Program Pi | Programm Raspberri Pi |  | software.engineer@university.org
Program Pi | Develop Use Cases |  | software.engineer@university.org
Project | Project Management |  | project.manager@university.org
Prototype | Present Concept |  | manufacturing.engineer@university.org
Prototype | Prepare Presentation |  | manufacturing.engineer@university.org
Prototype | Manufacturing Cost Analysis |  | manufacturing.engineer@university.org
Project | Software Development |  | project.manager@university.org
Project | Harware development |  | project.manager@university.org

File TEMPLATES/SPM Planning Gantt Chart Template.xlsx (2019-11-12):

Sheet: Gantt_Planned
Date | 2017-10-10 | 2017-10-17 | 2017-10-24 | 2017-10-31 | 2017-11-07 | 2017-11-14 | 2017-11-21 | 2017-11-28 | 2017-12-05 | 2017-12-12 | 2017-12-19 | 2017-12-26 | 2017-01-02 | 2017-01-09 | 2017-01-16 | 2017-01-23 | 2017-01-30 | 2017-02-06 | 2017-02-13 | 2017-02-20 | 2017-02-27 | 2017-03-06 | TASK TOTAL | SUB TOTAL
Week | 1 | 2 | 3 | 4 | 5 | 6 | 7 | 8 | 9 | 10 | 11 | 12 | 13 | 14 | 15 | 16 | 17 | 18 | 19 | 20 | 21 | 22 |  | Contingency | Responsible | Contributor1 | Contributor2
Workload | 48 | 48 | 48 | 48 | 48 | 48 | 48 | 48 | 48 | 48 | 48 | 48 | 48 | 48 | 48 | 48 | 48 | 48 | 48 | 48 | 48 | 48 | 1056 | 144 | project.manager@university.org | MarketingToBeNamed@university.org
Project Management |  |  |  |  |  |  |  |  |  |  |  |  |  |  |  |  |  |  |  |  |  |  |  | 114 | project.manager@university.org | MarketingToBeNamed@university.org
Initiation | 16 | 4 |  |  |  |  |  |  |  |  |  |  |  |  |  |  |  |  |  |  |  |  | 20 |  | project.manager@university.org | MarketingToBeNamed@university.org
Planning | 16 | 12 | 12 | 12 |  |  |  |  |  |  |  |  |  |  |  |  |  |  |  |  |  |  | 52 |  | project.manager@university.org | MarketingToBeNamed@university.org
Monitoring | 2 | 2 | 2 | 2 | 2 | 2 | 2 | 2 | 2 | 2 | 2 | 2 | 2 | 2 | 2 | 2 | 2 | 2 | 2 | 2 | 2 |  | 42 |  | project.manager@university.org | MarketingToBeNamed@university.org
Market Analysis |  | 16 | 8 |  |  |  |  |  |  |  |  |  |  |  |  |  |  |  |  |  |  |  | 24 | 96 | project.manager@university.org | MarketingToBeNamed@university.org
Competitor analysis |  |  | 4 | 12 |  |  |  |  |  |  |  |  |  |  |  |  |  |  |  |  |  |  | 16 |  | project.manager@university.org | MarketingToBeNamed@university.org
Customer analysis |  |  |  |  | 8 | 8 |  |  |  |  |  |  |  |  |  |  |  |  |  |  |  |  | 16 |  | project.manager@university.org | MarketingToBeNamed@university.org
Supplier analysis |  |  |  |  | 8 | 8 |  |  |  |  |  |  |  |  |  |  |  |  |  |  |  |  | 16 |  | project.manager@university.org | MarketingToBeNamed@university.org
Present Concept |  |  |  |  |  |  | 24 |  |  |  |  |  |  |  |  |  |  |  |  |  |  |  | 24 |  | project.manager@university.org | MarketingToBeNamed@university.org
Harware development |  |  |  |  | 2 | 2 | 2 | 2 | 2 | 2 | 2 | 2 | 2 | 2 | 2 | 2 | 2 | 2 |  |  |  |  | 28 | 326 | designer.engineer@university.org | project.manager@university.org
Design Case |  |  |  |  | 16 | 16 | 8 |  |  |  |  |  |  |  |  |  |  |  |  |  |  |  | 40 |  | designer.engineer@university.org | project.manager@university.org | manufacturing.engineer@university.org
Print Prototype Case |  |  |  |  |  |  |  | 16 | 16 |  |  |  |  |  |  |  |  |  |  |  |  |  | 32 |  | designer.engineer@university.org | project.manager@university.org | manufacturing.engineer@university.org
Review Design |  |  |  |  |  |  |  |  |  | 16 | 16 |  |  |  |  |  |  |  |  |  |  |  | 32 |  | designer.engineer@university.org | project.manager@university.org | manufacturing.engineer@university.org
Research Manufacturing Options |  |  |  |  |  |  |  | 14 | 14 | 14 | 14 | 14 |  |  |  |  |  |  |  |  |  |  | 70 |  | designer.engineer@university.org | project.manager@university.org | manufacturing.engineer@university.org
Research Power Supply |  |  |  |  |  |  |  |  |  |  |  | 8 |  |  |  |  |  |  |  |  |  |  | 8 |  | designer.engineer@university.org | project.manager@university.org | manufacturing.engineer@university.org
Select Power Supply |  |  |  |  |  |  |  |  |  |  |  |  | 8 |  |  |  |  |  |  |  |  |  | 8 |  | designer.engineer@university.org | project.manager@university.org | manufacturing.engineer@university.org
Research Power Button |  |  |  |  |  |  |  |  |  |  |  |  | 8 |  |  |  |  |  |  |  |  |  | 8 |  | designer.engineer@university.org | project.manager@university.org | manufacturing.engineer@university.org
Select Power Button |  |  |  |  |  |  |  |  |  |  |  |  |  | 8 |  |  |  |  |  |  |  |  | 8 |  | designer.engineer@university.org | project.manager@university.org | manufacturing.engineer@university.org
Research Volume Button |  |  |  |  |  |  |  |  |  |  |  |  | 8 |  |  |  |  |  |  |  |  |  | 8 |  | designer.engineer@university.org | project.manager@university.org | manufacturing.engineer@university.org
Select Volume Button |  |  |  |  |  |  |  |  |  |  |  |  |  | 8 |  |  |  |  |  |  |  |  | 8 |  | designer.engineer@university.org | project.manager@university.org | manufacturing.engineer@university.org
Research Loudspeaker |  |  |  |  |  |  |  |  |  |  |  |  |  | 10 |  |  |  |  |  |  |  |  | 10 |  | designer.engineer@university.org | project.manager@university.org | manufacturing.engineer@university.org
Select Loudspeaker |  |  |  |  |  |  |  |  |  |  |  |  |  |  | 10 |  |  |  |  |  |  |  | 10 |  | designer.engineer@university.org | project.manager@university.org | manufacturing.engineer@university.org
Design Internal Connectors |  |  |  |  |  |  |  |  |  |  |  |  |  |  | 16 | 8 |  |  |  |  |  |  | 24 |  | designer.engineer@university.org | project.manager@university.org | manufacturing.engineer@university.org
Case Durability / FEA |  |  |  |  |  |  |  |  |  |  |  |  |  |  |  | 8 | 8 | 16 |  |  |  |  | 32 |  | designer.engineer@university.org | project.manager@university.org | manufacturing.engineer@university.org
Software Development | 6 | 6 | 2 | 2 | 2 | 2 | 2 | 2 | 2 | 2 | 2 | 2 | 2 | 2 | 2 | 2 | 2 |  |  |  |  |  | 42 | 278 | programmer.engineer@university.org | electronics.engineer@university.org | project.manager@university.org
Research Software Plattforms |  |  | 12 | 12 |  |  |  |  |  |  |  |  |  |  |  |  |  |  |  |  |  |  | 24 |  | programmer.engineer@university.org | electronics.engineer@university.org | project.manager@university.org
Research Raspberry Pi Alternatives |  |  |  |  | 2 | 2 | 2 |  |  |  |  |  |  |  |  |  |  |  |  |  |  |  | 6 |  | programmer.engineer@university.org | electronics.engineer@university.org | project.manager@university.org
Develop Connection Scenarios |  |  |  |  |  |  |  | 4 | 4 | 4 |  |  |  |  |  |  |  |  |  |  |  |  | 12 |  | programmer.engineer@university.org | electronics.engineer@university.org | project.manager@university.org
Develop Use Cases |  |  |  |  |  |  |  |  |  |  | 4 | 12 | 10 |  |  |  |  |  |  |  |  |  | 26 |  | programmer.engineer@university.org | electronics.engineer@university.org | project.manager@university.org
Evaluate App Options |  |  |  |  |  |  |  |  |  |  |  |  |  | 8 | 8 | 8 | 8 |  |  |  |  |  | 32 |  | programmer.engineer@university.org | electronics.engineer@university.org | project.manager@university.org
Raspberri Pi - OS familarisation | 8 | 8 |  |  |  |  |  |  |  |  |  |  |  |  |  |  |  |  |  |  |  |  | 16 |  | programmer.engineer@university.org | electronics.engineer@university.org | project.manager@university.org
Raspberri Pi - IO Interfaces |  |  | 8 | 8 | 8 |  |  |  |  |  |  |  |  |  |  |  |  |  |  |  |  |  | 24 |  | programmer.engineer@university.org | electronics.engineer@university.org | project.manager@university.org
Raspberri Pi - Networking |  |  |  |  |  | 8 | 8 | 8 |  |  |  |  |  |  |  |  |  |  |  |  |  |  | 24 |  | programmer.engineer@university.org | electronics.engineer@university.org | project.manager@university.org
Raspberri Pi - Programming |  |  |  |  |  |  |  |  | 8 | 8 | 8 | 8 | 8 | 8 | 8 | 8 | 8 |  |  |  |  |  | 72 |  | programmer.engineer@university.org | electronics.engineer@university.org | project.manager@university.org
Prototyping and Finalising |  |  |  |  |  |  |  |  |  |  |  |  |  |  |  | 2 | 2 | 2 | 2 | 2 | 2 |  | 12 | 242 | manufacturing.engineer@university.org | designer.engineer@university.org | software.engineer@university.org
Print and Assemble Prototype |  |  |  |  |  |  |  |  |  |  |  |  |  |  |  | 8 | 8 | 16 |  |  |  |  | 32 |  | manufacturing.engineer@university.org | designer.engineer@university.org | software.engineer@university.org
Raspberri Pi Prototype Troubleshooting |  |  |  |  |  |  |  |  |  |  |  |  |  |  |  |  | 8 | 10 | 8 |  |  |  | 26 |  | manufacturing.engineer@university.org | designer.engineer@university.org | software.engineer@university.org
Manufacturing Cost Analysis |  |  |  |  |  |  |  |  |  |  |  |  |  |  |  |  |  |  | 16 | 10 |  |  | 26 |  | manufacturing.engineer@university.org | designer.engineer@university.org | software.engineer@university.org
Simulate Assembly Automation |  |  |  |  |  |  |  |  |  |  |  |  |  |  |  |  |  |  | 16 | 10 |  |  | 26 |  | manufacturing.engineer@university.org | designer.engineer@university.org | software.engineer@university.org
Prepare Presentation |  |  |  |  |  |  |  |  |  |  |  |  |  |  |  |  |  |  | 4 | 12 | 20 |  | 36 |  | manufacturing.engineer@university.org | designer.engineer@university.org | software.engineer@university.org
Prepare Project Report |  |  |  |  |  |  |  |  |  |  |  |  |  |  |  |  |  |  |  | 12 | 24 | 48 | 84 |  | manufacturing.engineer@university.org | designer.engineer@university.org | software.engineer@university.org
 |  |  |  |  |  |  |  |  |  |  |  |  |  |  |  |  |  |  |  |  |  |  | 1056 | 1056

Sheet: Contacts
FirstName | FamilyName | Email | Organisation | Phone | Mobile | Address
Oliver | Vogt | oliver.vogt@university.org | EngineeringCompany
Designer | Engineer | designer.engineer@university.org | EngineeringCompany
Programmer | Engineer | programmer.engineer@university.org | EngineeringCompany
Manufacturing | Engineer | manufacturing.engineer@university.org | EngineeringCompany
Director | ToBeNamed | DirectorToBeNamed@university.org | EngineeringCompany
Marketing | ToBeNamed | MarketingToBeNamed@university.org | EngineeringCompany
Finance | ToBeNamed | FinanceToBeNamed@university.org | EngineeringCompany
Bank | ToBeNamed | BankToBeNamed@university.org | Lloyds Bank
S-Customer | standard | S-CustomerToBeNamed@university.org | Rapid Electonics
Adv-Customer | advanced | Adv-CustomerToBeNamed@university.org | Amazon
Retailer | ToBeNamed | RetailerToBeNamed@university.org | Carphone Warehouse
Wholesaler | ToBeNamed | WholesalerToBeNamed@university.org | Amazon
IT-Support | ToBeNamed | IT-SupportToBeNamed@university.org | Waterstone Consultancy
Design | Tutor1 | design.tutor1@university.org | Waterstone Consultancy
Design | Tutor2 | design.tutor2@university.org | Waterstone Consultancy
software | engineer | software.engineer@university.org | EngineeringCompany
electronics | engineer | electronics.engineer@university.org | EngineeringCompany
project | manager | project.manager@university.org | EngineeringCompany
Project | Sponsot | project.sponsor@company.com | Lloyds Bank

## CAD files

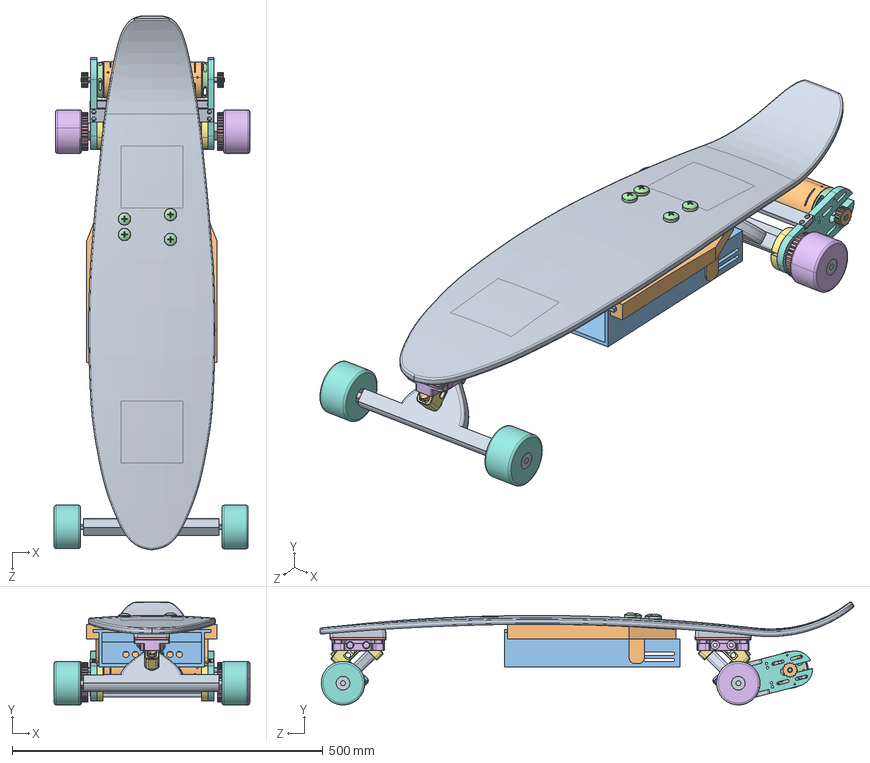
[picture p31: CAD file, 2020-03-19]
CAD files/Assemblies/BoardAndRail_v2.SLDASM
314.6 x 165.6 x 859.0 mm
ESB_Board_Padded(For Completion)
Battery_Railing_v2
Battery_Box_v2
pan cross head_am x 4
hex nut style 1_am x 4
baseplate part1.STEP x 2
baseplate part 2.STEP x 2
pivot.STEP x 2
hanger.STEP x 2
kingpin.STEP x 2
kingpin nut.STEP x 2
bushing.STEP x 8
spacer.STEP x 2
hex bolt gradec_bsi_BS EN 24016 - M6 x 40 x 18-WN.STEP x 2
hex nut style 1 gradeab_bsi_BS EN 24032 - M6 - W - N.STEP x 2
Wheel_CAD x 2
bearing x 4
Part2.stp.step x 2
Part3.stp.step x 2
Part1.stp.step x 2
Wheel_Cog2_CAD.STEP x 2
Wheel_CAD.STEP x 2
clamp.step x 2
Side Panel.step x 2
improved support bar.step x 2
Motor_Cog.step x 2

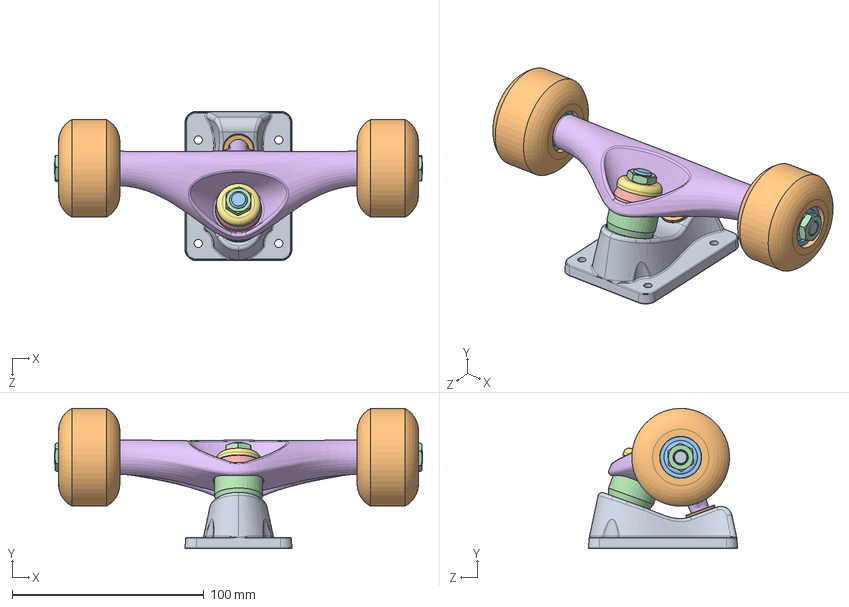
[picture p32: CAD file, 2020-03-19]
CAD files/Assemblies/ESB_Board Downloaded Trucks/User Library-SADC - QuachDaiThanh - Skateboard - Truck Sub-Assembly.SLDASM
192.0 x 73.1 x 77.9 mm
User Library-SADC - QuachDaiThanh - Skateboard - Truck Sub-Assembly_SADC - QuachDaiThanh - Skateboard - BASEPLATE
User Library-SADC - QuachDaiThanh - Skateboard - Truck Sub-Assembly_SADC - QuachDaiThanh - Skateboard - PIVOT BISHING
User Library-SADC - QuachDaiThanh - Skateboard - Truck Sub-Assembly_SADC - QuachDaiThanh - Skateboard - KINGPIN
User Library-SADC - QuachDaiThanh - Skateboard - Truck Sub-Assembly_SADC - QuachDaiThanh - Skateboard - BUSHING
User Library-SADC - QuachDaiThanh - Skateboard - Truck Sub-Assembly_SADC - QuachDaiThanh - Skateboard - CONE BUSHING
User Library-SADC - QuachDaiThanh - Skateboard - Truck Sub-Assembly_SADC - QuachDaiThanh - Skateboard - HANGER
User Library-SADC - QuachDaiThanh - Skateboard - Truck Sub-Assembly_SADC - QuachDaiThanh - Skateboard - TOP CUP WASHER
User Library-SADC - QuachDaiThanh - Skateboard - Truck Sub-Assembly_SADC - QuachDaiThanh - Skateboard - WASHER x 4
User Library-SADC - QuachDaiThanh - Skateboard - Truck Sub-Assembly_SADC - QuachDaiThanh - Skateboard - axle
User Library-SADC - QuachDaiThanh - Skateboard - Truck Sub-Assembly_SADC - QuachDaiThanh - Skateboard - WHEEL x 2
instrument ball bearing_68_am x 4
hex nut jam_am x 3

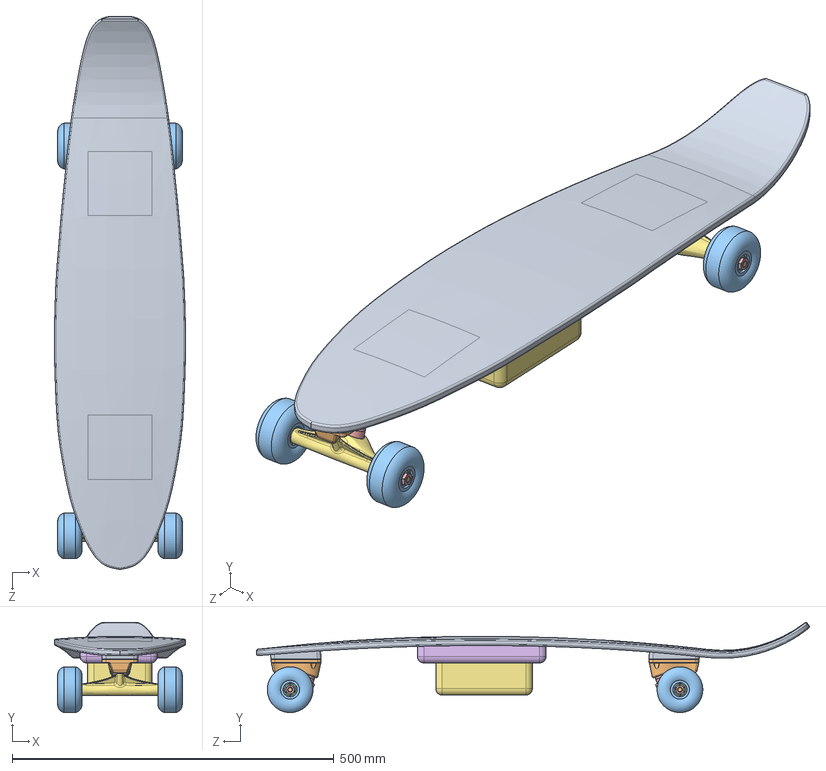
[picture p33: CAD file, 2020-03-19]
CAD files/Support Files/Board CAD/Concept_E.SLDASM
203.9 x 140.0 x 859.0 mm
ESB_Board_Padded(Only for trucks)
User Library-SADC - QuachDaiThanh - Skateboard - Truck Sub-Assembly_SADC - QuachDaiThanh - Skateboard - BASEPLATE x 2
User Library-SADC - QuachDaiThanh - Skateboard - Truck Sub-Assembly_SADC - QuachDaiThanh - Skateboard - PIVOT BISHING x 2
User Library-SADC - QuachDaiThanh - Skateboard - Truck Sub-Assembly_SADC - QuachDaiThanh - Skateboard - KINGPIN x 2
User Library-SADC - QuachDaiThanh - Skateboard - Truck Sub-Assembly_SADC - QuachDaiThanh - Skateboard - BUSHING x 2
User Library-SADC - QuachDaiThanh - Skateboard - Truck Sub-Assembly_SADC - QuachDaiThanh - Skateboard - CONE BUSHING x 2
User Library-SADC - QuachDaiThanh - Skateboard - Truck Sub-Assembly_SADC - QuachDaiThanh - Skateboard - HANGER x 2
User Library-SADC - QuachDaiThanh - Skateboard - Truck Sub-Assembly_SADC - QuachDaiThanh - Skateboard - TOP CUP WASHER x 2
User Library-SADC - QuachDaiThanh - Skateboard - Truck Sub-Assembly_SADC - QuachDaiThanh - Skateboard - WASHER x 8
User Library-SADC - QuachDaiThanh - Skateboard - Truck Sub-Assembly_SADC - QuachDaiThanh - Skateboard - axle x 2
User Library-SADC - QuachDaiThanh - Skateboard - Truck Sub-Assembly_SADC - QuachDaiThanh - Skateboard - WHEEL x 4
instrument ball bearing_68_am x 8
hex nut jam_am x 6
ESB_fillerBattery
ESB_fillerMotorBox

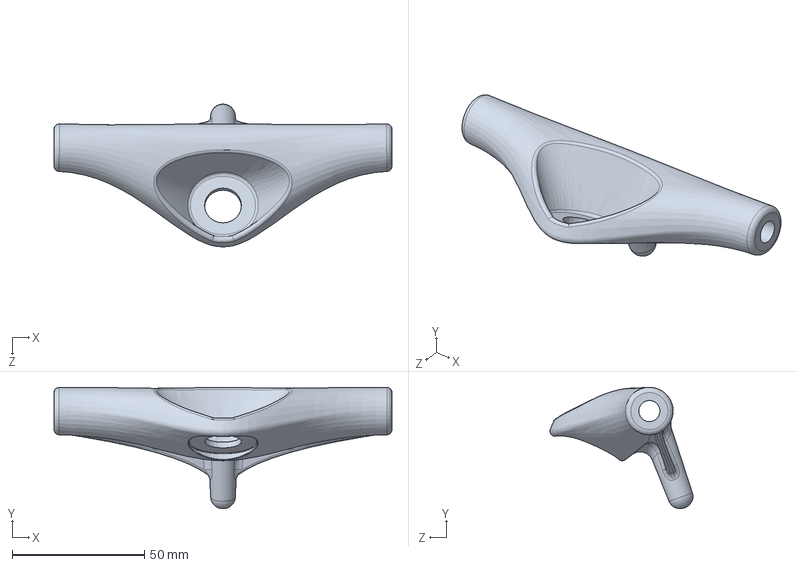
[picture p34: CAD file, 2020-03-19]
CAD files/Support Files/Board CAD/Downloaded Trucks/User Library-SADC - QuachDaiThanh - Skateboard - Truck Sub-Assembly_SADC - QuachDaiThanh - Skateboard - HANGER.SLDPRT
128.0 x 46.0 x 54.1 mm

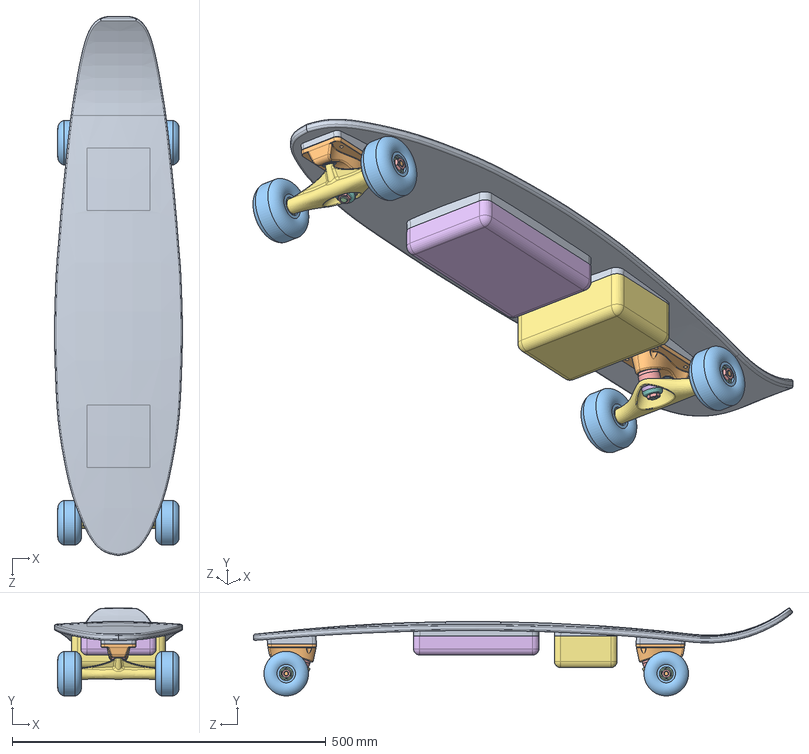
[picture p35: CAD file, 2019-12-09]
FEASIBILITY STUDY/Board/L2 Design CAD/Assemblies/ESB_Total Assembly.SLDASM
203.9 x 140.0 x 859.0 mm
ESB_Board_Padded
User Library-SADC - QuachDaiThanh - Skateboard - Truck Sub-Assembly_SADC - QuachDaiThanh - Skateboard - BASEPLATE x 2
User Library-SADC - QuachDaiThanh - Skateboard - Truck Sub-Assembly_SADC - QuachDaiThanh - Skateboard - PIVOT BISHING x 2
User Library-SADC - QuachDaiThanh - Skateboard - Truck Sub-Assembly_SADC - QuachDaiThanh - Skateboard - KINGPIN x 2
User Library-SADC - QuachDaiThanh - Skateboard - Truck Sub-Assembly_SADC - QuachDaiThanh - Skateboard - BUSHING x 2
User Library-SADC - QuachDaiThanh - Skateboard - Truck Sub-Assembly_SADC - QuachDaiThanh - Skateboard - CONE BUSHING x 2
User Library-SADC - QuachDaiThanh - Skateboard - Truck Sub-Assembly_SADC - QuachDaiThanh - Skateboard - HANGER x 2
User Library-SADC - QuachDaiThanh - Skateboard - Truck Sub-Assembly_SADC - QuachDaiThanh - Skateboard - TOP CUP WASHER x 2
User Library-SADC - QuachDaiThanh - Skateboard - Truck Sub-Assembly_SADC - QuachDaiThanh - Skateboard - WASHER x 8
User Library-SADC - QuachDaiThanh - Skateboard - Truck Sub-Assembly_SADC - QuachDaiThanh - Skateboard - axle x 2
User Library-SADC - QuachDaiThanh - Skateboard - Truck Sub-Assembly_SADC - QuachDaiThanh - Skateboard - WHEEL x 4
instrument ball bearing_68_am x 8
hex nut jam_am x 6
ESB_fillerBattery
ESB_fillerMotorBox

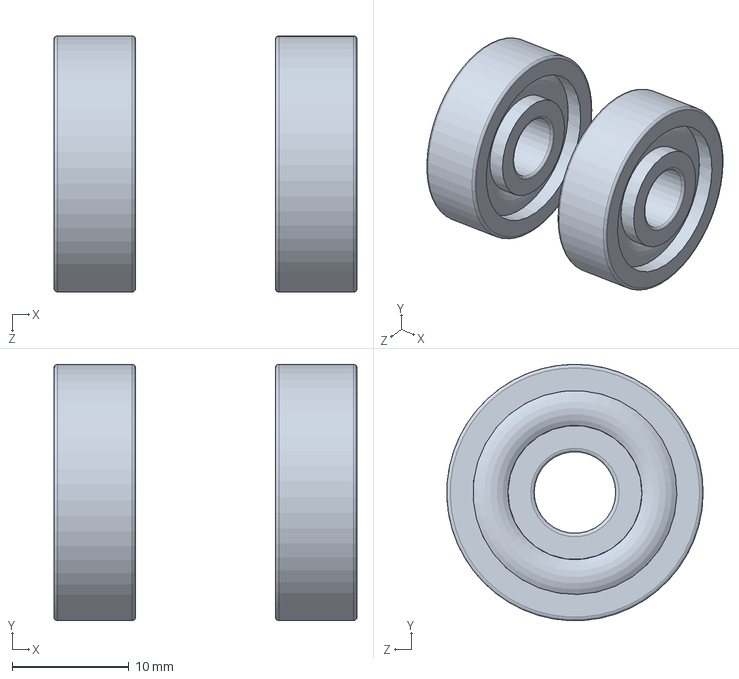
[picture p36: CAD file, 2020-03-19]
CAD files/Support Files/Board CAD/Downloaded Trucks/User Library-SADC - QuachDaiThanh - Skateboard - Truck Sub-Assembly_SADC - QuachDaiThanh - Skateboard - WHELL Assem.SLDASM
26.0 x 22.0 x 22.0 mm
instrument ball bearing_68_am x 2

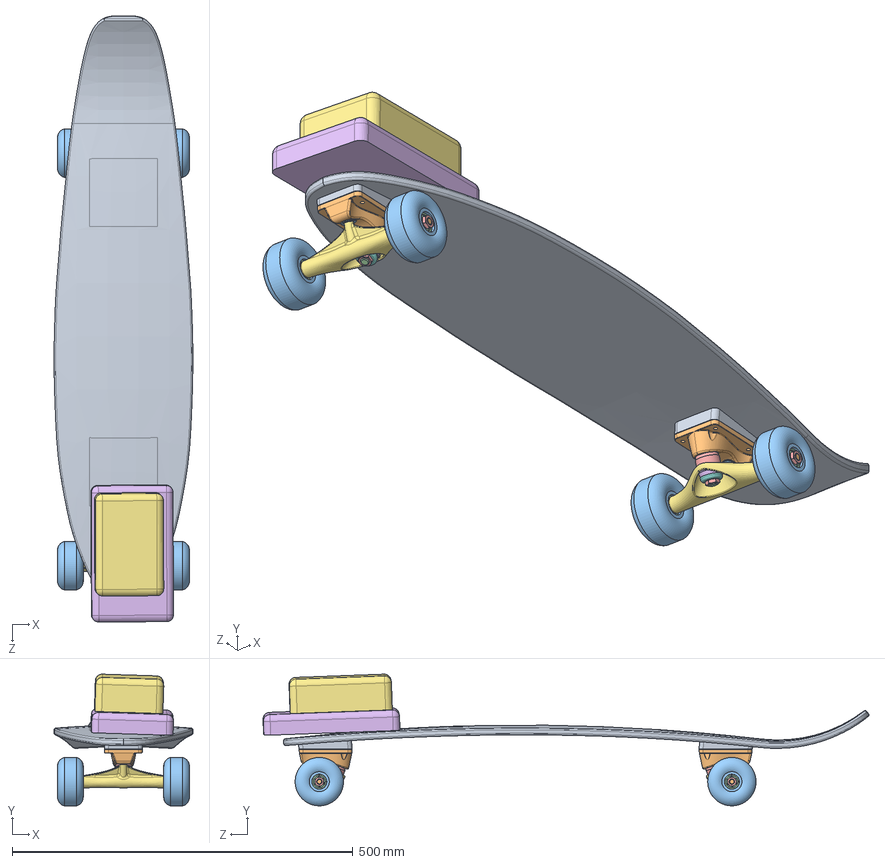
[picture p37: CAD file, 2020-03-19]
CAD files/Assemblies/Concept C.SLDASM
203.9 x 193.3 x 889.4 mm
ESB_Board_Padded(Only for trucks)
User Library-SADC - QuachDaiThanh - Skateboard - Truck Sub-Assembly_SADC - QuachDaiThanh - Skateboard - BASEPLATE x 2
User Library-SADC - QuachDaiThanh - Skateboard - Truck Sub-Assembly_SADC - QuachDaiThanh - Skateboard - PIVOT BISHING x 2
User Library-SADC - QuachDaiThanh - Skateboard - Truck Sub-Assembly_SADC - QuachDaiThanh - Skateboard - KINGPIN x 2
User Library-SADC - QuachDaiThanh - Skateboard - Truck Sub-Assembly_SADC - QuachDaiThanh - Skateboard - BUSHING x 2
User Library-SADC - QuachDaiThanh - Skateboard - Truck Sub-Assembly_SADC - QuachDaiThanh - Skateboard - CONE BUSHING x 2
User Library-SADC - QuachDaiThanh - Skateboard - Truck Sub-Assembly_SADC - QuachDaiThanh - Skateboard - HANGER x 2
User Library-SADC - QuachDaiThanh - Skateboard - Truck Sub-Assembly_SADC - QuachDaiThanh - Skateboard - TOP CUP WASHER x 2
User Library-SADC - QuachDaiThanh - Skateboard - Truck Sub-Assembly_SADC - QuachDaiThanh - Skateboard - WASHER x 8
User Library-SADC - QuachDaiThanh - Skateboard - Truck Sub-Assembly_SADC - QuachDaiThanh - Skateboard - axle x 2
User Library-SADC - QuachDaiThanh - Skateboard - Truck Sub-Assembly_SADC - QuachDaiThanh - Skateboard - WHEEL x 4
instrument ball bearing_68_am x 8
hex nut jam_am x 6
ESB_fillerBattery
ESB_fillerMotorBox

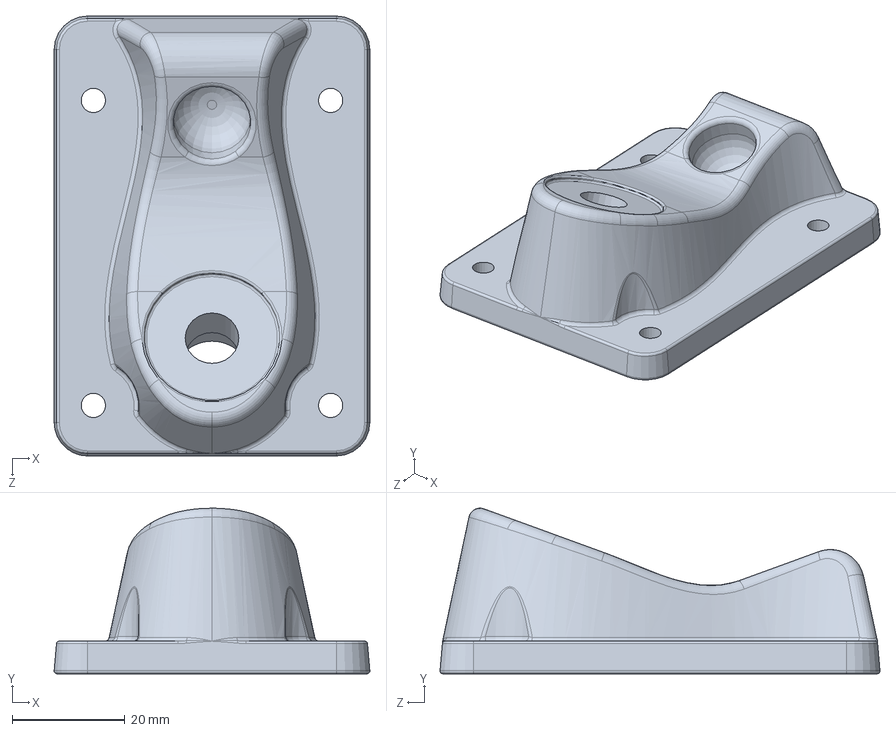
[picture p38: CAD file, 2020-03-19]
CAD files/Assemblies/ESB_Board Downloaded Trucks/User Library-SADC - QuachDaiThanh - Skateboard - Truck Sub-Assembly_SADC - QuachDaiThanh - Skateboard - BASEPLATE.SLDPRT
55.9 x 29.3 x 77.9 mm

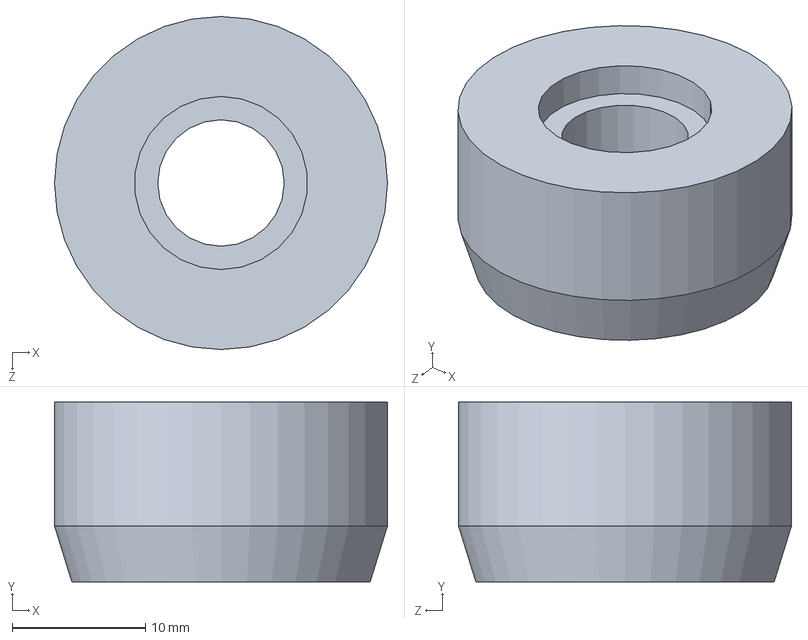
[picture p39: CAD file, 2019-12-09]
CAD files/Assemblies/ESB_Board Downloaded Trucks/User Library-SADC - QuachDaiThanh - Skateboard - Truck Sub-Assembly_SADC - QuachDaiThanh - Skateboard - BUSHING.SLDPRT
25.0 x 13.5 x 25.0 mm

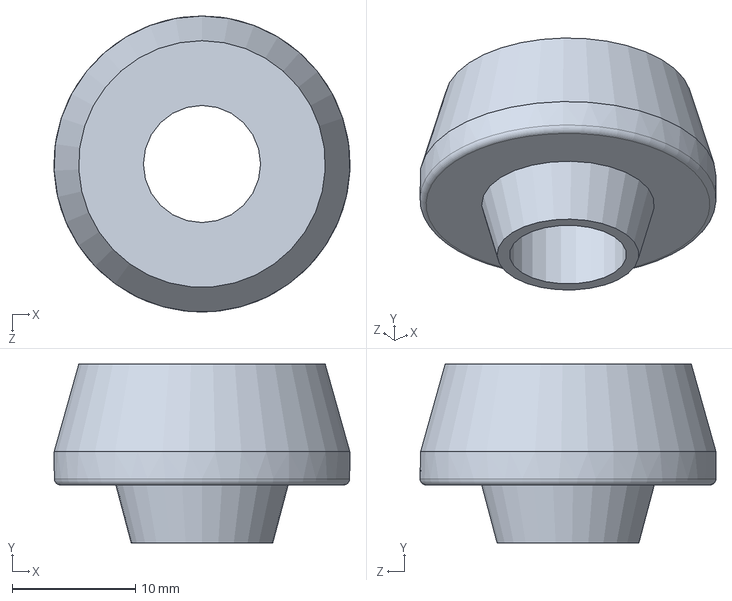
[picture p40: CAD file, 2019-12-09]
CAD files/Assemblies/ESB_Board Downloaded Trucks/User Library-SADC - QuachDaiThanh - Skateboard - Truck Sub-Assembly_SADC - QuachDaiThanh - Skateboard - CONE BUSHING.SLDPRT
24.0 x 14.5 x 24.0 mm

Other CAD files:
CAD files/Assemblies/Concept D.SLDASM
CAD files/Support Files/Board CAD/Concept_D.SLDASM
CAD files/Assemblies/Concept A.SLDASM
CAD files/Support Files/Board CAD/Concept_A.SLDASM
CAD files/Support Files/Board CAD/Downloaded Trucks/User Library-SADC - QuachDaiThanh - Skateboard - Truck Sub-Assembly.SLDASM
CAD files/Assemblies/Belt1-1.sldprt
CAD files/Assemblies/Belt2-2.sldprt
CAD files/Assemblies/BoardAndRail.SLDASM
CAD files/Assemblies/CompledSkate.SLDASM
CAD files/Assemblies/Concept B.SLDASM
CAD files/Assemblies/ESB_Board Downloaded Trucks/User Library-SADC - QuachDaiThanh - Skateboard - Truck Sub-Assembly_Hex Nut Jam_AM.SLDPRT
CAD files/Assemblies/ESB_Board Downloaded Trucks/User Library-SADC - QuachDaiThanh - Skateboard - Truck Sub-Assembly_Instrument Ball Bearing_68_AM.sldprt
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

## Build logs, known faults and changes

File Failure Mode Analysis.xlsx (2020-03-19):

SUBSYSTEM | FAILURE MODE | EFFECT |  |  | MITIGATION
 |  |  | Likelihood? | Severity
Battery Cells | Mechanical Damage | Explodes, fire, capacity reduction. | High | Very High | Hard Casing, anti-vibration (reduce metal fatigue/work hardening).
 | Over Charging | Decreased Capacity, fire, explosion, expansion due to CO2. | High | Very High | Fuses, Smart Charger, detailed user manual, battery health monitor.
 | Over Discharge | Decreased Capacity, expansion due to CO2, metal whisker salt deposits, self-discharge leading to remedial charging. | Medium | Medium | Fuses, Anti-short connectors, idle mode, battery monitor, hibernation, isolation switch.
 | Terminal Short | Very Large current draw, heating, fire, all other components downstream lose power. | Low | Very High | Use industry standard connectors, isolated contacts - no naked contacts, waterproofing, design to prevent shorts due to circuit failure, fuses in series with battery.
MUX Micro | Parallel and Series control lines both on | Terminal Short. | Low | High | Staggered switching to account for switching time.
 | Load Switches failing into a short | Terminal Short. | Low | High | Fuse blows, protects circuit.
 | Load Switches failing into an open | No Effect, As is the system is in idle mode. | Low | Low | Heartbeat does not begin - display error code on LEDs.
 | Loses Power | Falls through to idle mode, battery pack is isolated. | Medium | Low | Specify the coin battery to sufficient capacity to meet maintenance lifespan.
 | Current or Voltage Sensor Fails | Micro acts as if there is no battery present, (appears to be in hibernation mode). | Low | Low | If only one of the two sensors are broken then there must be an error - display error codes on LEDs.
Microcontroller | Load Cell/Load Cell connections fail | No voltage appears on analogue inputs. | Low | Low | System cannot determine the weight of the user – turn of heartbeat and display error on LCD.
 | Power Supply/Power supply connection Fails | Arduino shuts down, ESCs stop receiving PWM signals. | Low | Low | Using a heartbeat system, if the MUX Micro does not hear from the Arduino for a certain period, shuts down the board into idle mode.
 | Loss of report from hall effect sensors | Arduino loses speed of rotation information, cannot track distance travelled or whether the motors are spinning. | Low | Medium | If hall sensor information is lost - stop the motors and display error on LCD.
 | Connections to motors fail | ESCs stop receiving PWM signals. | Low | Low | ESCs will disarm, board coasts to a stop.
 | LCD fails | User no longer receives status information of the system. | Low | Low | N/A – Not affecting rest of system.
 | Buzzer fails | User no longer receives alerts from the system. | Low | Low | N/A – Not affecting rest of system.
 | headlight LEDs fail | User can no longer see where they are going in the dark. | Low | Medium | N/A – Not affecting rest of system.
ESCs | Loss of power | ESCs can no longer drive the motors. | Low | Medium | ESCs will disarm, board coasts to a stop.
 | Loss of /Bad PWM signal | ESCs no longer know what speed to turn at. | Low | Medium | ESCs will disarm, board coasts to a stop.
 | Hall sensor /connection fails | ESCs no longer know what speed the motor is turning at by direct measurement. | Low | Low | ESC changes to a mode where the rotation speed is inferred from inductive effects. Stops the motors as per above.
 | Internal Circuitry Fails | Could lead to fire, damage to motors. | Low | High | Use module within the specified current and voltage ratings.
 | Overheating | Damage to the circuitry, fire. | Low | High | Ensure proper airflow to the heatsinks.

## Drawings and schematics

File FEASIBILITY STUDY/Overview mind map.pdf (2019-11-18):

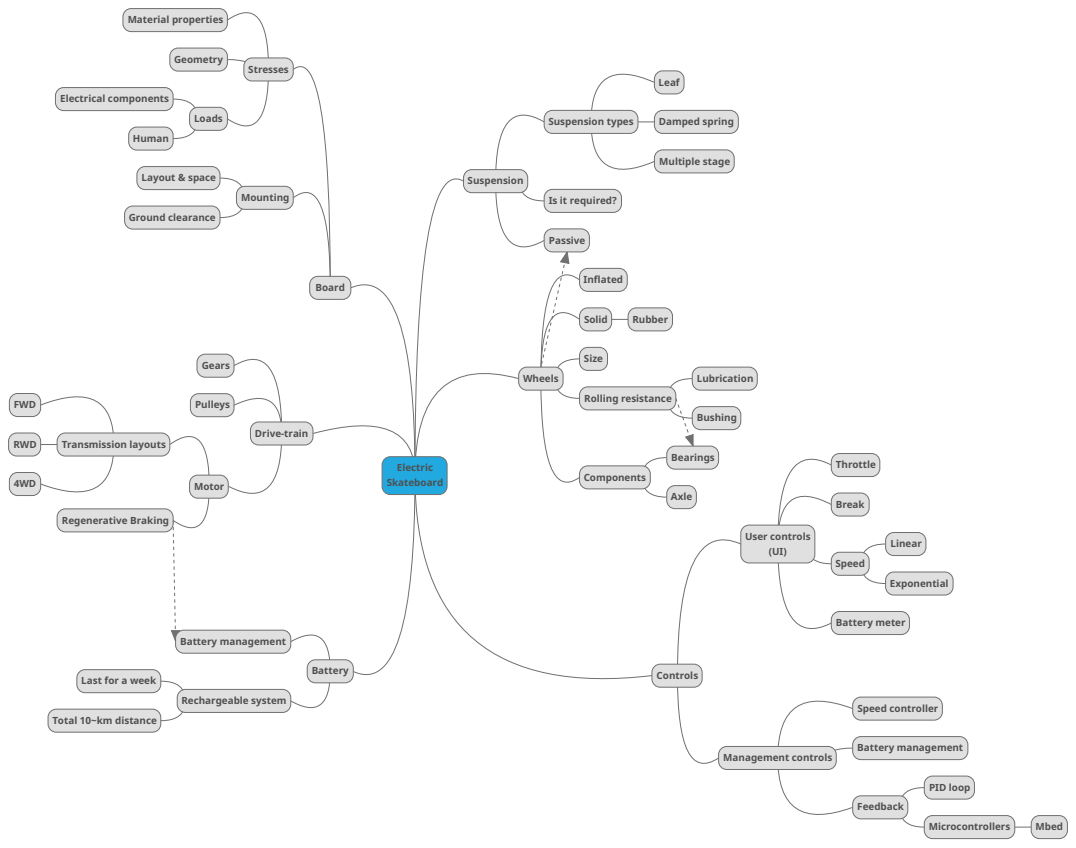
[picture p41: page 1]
Electric Skateboard; Board; Stresses; Material properties; Geometry; Loads; Electrical components; Human; Mounting; Layout & space; Ground clearance; Drive-train; Gears; Pulleys; Motor; Transmission layouts; FWD; RWD; Regenerative Braking; Battery; Battery management; Rechargeable system; Suspension; Suspension types; Leaf; Damped spring; Multiple stage; Passive; Wheels; Inflated; Solid; Rubber; Size; Rolling resistance; Lubrication; Bushing; Components; Bearings; Axle; Controls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

Is it required?

Last for a week

Total 10~km distance

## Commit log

2019-11-07 Added preliminalry motor writeup
2019-11-08 Added battery, update motor
2019-11-12 Updated motor writeup
2019-11-12 Add battery writeup
2019-11-12 Folder Restructure
    Folder restructure, with weekly minutes added
    [SPM Monitoring Gantt_simple_v03.xlsx, SPM Monitoring Gantt_with_EVM_v03.xlsm, SPM Planning Gantt Chart Template.xlsx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]
2019-11-15 Add route, and improved battery report
2019-11-18 Minor change to battery write
2019-11-18 New drivetrain report
2019-11-18 Added Gant chart
    [Gantt Chart.xlsx]
2019-11-19 Motor write
2019-11-19 Battery writeup
2019-11-25 Motor writeup
2019-11-26 Minor motor updates
2019-11-26 Added Torque calculation
2019-11-26 Updated battery writeup
2019-11-26 Added power calculation
2019-12-02 Updated charging, and lifespan
2019-12-03 Added CAD
    Added CAD
    [7804K146_STAINLESS STEEL BALL BEARING.SLDPRT, EBoard_Board.SLDPRT, EBoard_Board_backup.SLDPRT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]
2019-12-05 attempting to cut down
2019-12-08 Updated capacity sections
2019-12-09 Add files via upload
    Calculations updated to account for interaction between axle friction and rolling resistance
2019-12-09 Further Cutting, added schematic figure
2019-12-09 updated Drivetrain Report
2019-12-11 Create Pressure Pads Labelled.png
2019-12-11 Added Powertrain Immages
2019-12-11 updated Board images
2019-12-11 Updated Board images again
2019-12-12 larger drivetrain image font
2019-12-12 Wheels Eqns
2019-12-12 motor curve
2020-01-27 Added numerical battery spec
    [BatterySpec.xlsx]
2020-01-28 Added specifications
    [Powertrain-Spec.xlsx, Spec combined.xlsx]
2020-02-04 Added weekly meetings
    [Spec combined.xlsx]
2020-02-04 Design Matrix Used in Sunday Meeting
    [FWD_RWD_AWD_Design_Matrix.xlsx]
2020-02-05 Gantt Chart Update
    [Gantt Chart.xlsx]
2020-02-05 Updated Gantt Chart
    [Monitoring Gantt Chart.xlsx]
2020-02-05 Prelim battery charging stuff
2020-02-07 Added battery design
2020-02-10 Spec battery capacity update
    [Spec combined.xlsx]
2020-02-10 Updated battery design pdn
2020-02-10 Battery control circuits and diag update
2020-02-11 Updated battery presentation
2020-02-11 Updated flow diagrams
2020-02-13 Added Failure Mode Analysis
    [Failure Mode Analysis.xlsx]
2020-02-14 Added battery overview and schamtics
2020-02-15 Removed example presentation from tracking
    [Failure Mode Analysis.xlsx]
2020-02-15 Updated battery schematic
2020-02-16 Pulled better battery from poor merge
2020-02-17 Create Battery switch detailed.pdn
2020-02-17 Update Failure Mode Analysis.xlsx
    [Failure Mode Analysis.xlsx]
2020-02-17 Create Battery circuit better.pdn
2020-02-17 Updated the better circuit diag
2020-03-02 Added battery key points
2020-03-03 Updated battery points
2020-03-04 Added PBR render materials
2020-03-06 Battery md
2020-03-06 First Draft of Business Case
2020-03-07 Updated charger
2020-03-09 Updated Business Case
2020-03-14 cad
    Anson: Nyong
    [Battery_Box_v1.SLDPRT, Battery_Box_v2.SLDPRT, Battery_Box_v2_Analysis.SLDPRT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]
2020-03-17 Changed battery schematic serial line
2020-03-18 new cad
    [Battery_Box_v2.SLDPRT, Battery_Railing_v2.SLDPRT, Belt1-1.sldprt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]
2020-03-19 updated FMA
    [Failure Mode Analysis.xlsx]
2020-03-19 Added Packed CAD.zip
